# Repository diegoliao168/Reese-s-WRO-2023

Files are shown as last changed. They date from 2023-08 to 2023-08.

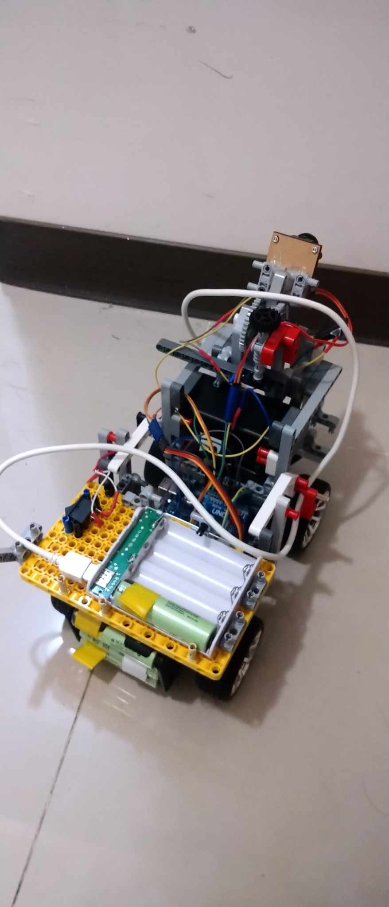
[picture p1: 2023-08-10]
v-photo/363670610_1052829679035555_8030239496635746678_n.jpg

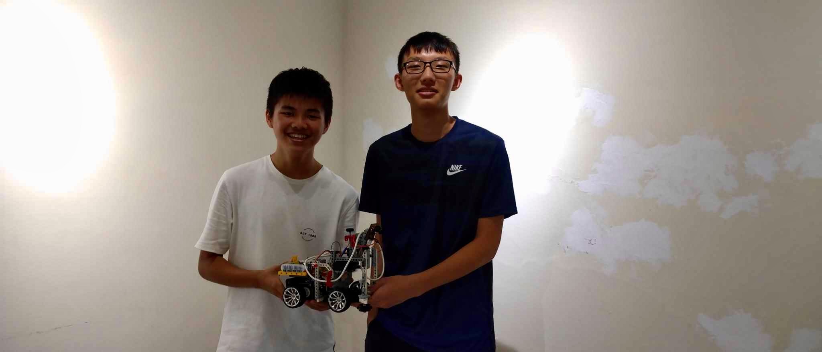
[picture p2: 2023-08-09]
t-photo/363800676_1494674244676651_163518513958916830_n.jpeg

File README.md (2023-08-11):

# Reese's

# 移動性管理

我們的機器人是採用與汽車相同的轉向邏輯和驅動方式。在前輪部分我們使用伺服馬達來控制我們的轉向機構，後輪的部分我們使用的是直流馬達。我們採用的是Arduino的Uno版和OpenMV的H7，Arduino的主要功用與控制轉向的伺服馬達溝通和後輪的直流馬達進行溝通。OpenMV的功用就像我們人的眼睛，透過影相辨識的方式來達到跟Arduino溝通控制車哪時轉向和哪時加速或減速。

在選擇馬達的時候我們找到兩種適合我們使用的馬達分別有4000rpm負載500公克的馬達和320rpm負載1500公克的馬達，考慮到我們的小車可能會需要拖動較大的載重。我們選擇了320rpm轉速的馬達負載1500公克的馬達。這顆馬達的型號為GA25-370、工作電壓六到十二伏特、功率2.5瓦、額定電流0.65安培、齒輪箱速比1:32.2。馬達之後有加速齒比帶動傳動軸來帶動後輪的兩顆輪子。

在前輪的部分我們選擇使用精準控制轉向角度的伺服馬達是MG996R。MG996R
工作電壓4.8V-7.2V、空載工作電流120mA。

因為一開始購買車輛的時候廠家沒有設計放電池的地方。因此我們3D列印了一塊在車子後的背板，為的就是能讓我們到電池有地方可以固定


# 電源和感測器管理
接下來是我們的車體結構是與市售的商家購買的，但是經過我們的改裝我們的車輛已經與市售的截然不同。我們車體裝上支架為了OpenMV和電池盒有辦法固定。應為電力不足得原因我們在車商裝了三套電池系統。第一套十二伏電池系統是供應主要的驅動馬達，接下來第二套八伏特的電池是供應給車上主要的溝通系統Arduino也是供應給前輪的轉向系統的伺服馬達，最後一套第三套四伏特的電池系統是給OpenMV單獨供電的為了讓OpenMV提供更穩定的訊息傳輸。

要讓我們與程式Arduino正確溝通我們需要Arduino IDE，Arduino IDE使與的程式語言是C語言透過C語言的溝通，我們的Arduino才能跟OpenMV和其他馬達傳送正確的指令。接下來OpenMV所使用的語言是Micro Python，Micro Python對我們來講是個全新的語言。當我們一開始使用的時候，我們一邊詢問我們的指導老師一遍看網路上的教學影片。開始撰寫OpenMV的程式從一開始的調顏色數值到顏色追蹤和如何用影像辨識距離。我們在寫OpenMV的程式時遇到最大的困難是在我們調顏色數值的時後，顏色數值可能會應為些微的燈光變化而有所不同。我們不得不反覆測試直到調到一個較好的數值。

原先我們使用的控制板是Arduino的Nano版經過我們的測試我們發現使用Nano版的時候Nano版的供電系統會不足以支撐兩顆馬達同時驅動，使轉向系統的伺服馬達無法轉到目標位子。經過測試後我們採用供電比較穩定的Arduino的Uno版，對支援更穩定的供電和更加優良的擴充。

經過我們的反覆測發現到原本8伏特的電池來去推動馬達的時後馬達的功率無法驅動我們的車。接下來我們就把原本的電壓乘以二到了十六伏特，但是我們沒有意識到我們所使用Arduino Uno的只能對應到十二伏特的電壓。應此我們燒壞了一塊主機板。經過這次經驗我們換了新的十二伏電池盒。也是因為改回了十二伏的電池，讓我們的機器人正常的執行任務，以及進行接下來的測試和實驗。

# 障礙管理
程式想法

先把轉彎角度、直走的速度、轉彎速度的角度都先歸零，直走伺服馬達的角度是固定的所以先放入變數還有每個顏色的閥值都是先量好放入變數，迴圈內的變數是每進行一次就要歸零。

當我們吧畫面正中央的第三等分跟第四等分來運算時我們可以透過畫面中的Y軸來判斷我們的車輛是否離牆面近而判斷是否轉彎並且修正。Y軸在畫面中越低就代表車輛離牆面越近，再來就傳送轉彎角度和馬達速度給Arduino Uno來進行轉彎。

如何判斷我們車輛應該轉逆時針還是順時針，我們運用到影像辨識來判斷橘色線的角度，大於90要轉左邊，小於90要轉右邊，這樣一來我們就可以知道每次轉彎是轉左邊還是右邊，但是影像辨識很容易受到燈光的影響，所以我們也試了很多方式來解決這個問題，也調了很多次閥值。

OpenMV
```
import sensor, image, time, math
from pyb import UART

threshold_index = 0

thresholds_black = [(38, 0, 100, -50, 74, -30)]
thresholds_red = [(8, 56, 127, 11, -128, 127)]
thresholds_green = [(25, 17, -24, -4, -28, 13)]
thresholds_blue = [(18, 45, 27, -7, -103, -7)]
thresholds_orange = [(47, 100, 71, 9, 127, -105)]

sensor.reset()
sensor.set_pixformat(sensor.RGB565)
sensor.set_framesize(sensor.QVGA)
sensor.skip_frames(time = 2000)
sensor.set_auto_gain(False)
sensor.set_auto_whitebal(False)
clock = time.clock()
uart = UART(3, 19200)
m = 0
angle = 0    #轉彎角度
mot_1 = 200  #轉彎PWM
mot_2 = 200   #直走PWM
middle = 95  #伺服馬達中間值

while(True):

    x3 = 0
    x4 = 0
    y3 = 0
    y4 = 0
    two_m = 0
    two = 0

    clock.tick()
    img = sensor.snapshot()
    #找橘色
    if m == 0 :
        for blob in img.find_blobs([thresholds_orange[0]], pixels_threshold=400, area_threshold=400, merge=True):

            if blob.elongation() > 0.5:
                #img.draw_edges(blob.min_corners(), color=(255,0,0))
                img.draw_line(blob.major_axis_line(), color=(0,255,0))
                print( blob.rotation_deg())    #把線的角度算出來
                m = blob.rotation_deg()    #方進m這個變數
                #img.draw_line(blob.minor_axis_line(), color=(0,0,255))
                print (m)
                print (clock)
                if m > 90:  #判斷要轉左邊還是右邊

                    angle = 65 #左
                else :
                    angle = 125 #右

    threemax_x = 0
    threemax_y = 0
    #畫面三找黑色並把他框出來
    for blob in img.find_blobs([thresholds_black[threshold_index]], pixels_threshold=200, area_threshold=200, merge=True,roi=(108,0,54,250)):

        '''
        if blob.elongation() > 0.5:
            img.draw_edges(blob.min_corners(), color=(255,0,0))
            img.draw_line(blob.major_axis_line(), color=(0,255,0))
            img.draw_line(blob.minor_axis_line(), color=(0,0,255))
        '''
        if blob.cy() > threemax_y:     #找出y最大的框
            threemax_x = blob.cx()
            threemax_y = blob.cy()
    img.draw_rectangle(blob.rect())
    img.draw_cross(blob.cx(), blob.cy())
    x3 = threemax_x
    y3 = threemax_y

    img.draw_keypoints([(blob.cx(), blob.cy(), int(math.degrees(blob.rotation())))], size=20)
    if  threemax_y > 100:
        uart.write(str(mot_1)+","+ str(angle)+"E\n")
        time.sleep_ms(20)
    else:
        uart.write(str(mot_2)+","+ str(middle)+"E\n")
        time.sleep_ms(20)

    fourmax_x = 0
    fourmax_y = 0
    #畫面四找黑色並把他框出來
    for blob in img.find_blobs([thresholds_black[threshold_index]], pixels_threshold=200, area_threshold=200, merge=True,roi=(162,0,54,250)):

        '''
        if blob.elongation() > 0.5:
            img.draw_edges(blob.min_corners(), color=(255,0,0))
            img.draw_line(blob.major_axis_line(), color=(0,255,0))
            img.draw_line(blob.minor_axis_line(), color=(0,0,255))
        '''
        if blob.cy() > fourmax_y:     #找出Y最大的框
            fourmax_x = blob.cx()
            fourmax_y = blob.cy()
    img.draw_rectangle(blob.rect())
    img.draw_cross(blob.cx(), blob.cy())
    x4 = fourmax_x
    y4 = fourmax_y
    if fourmax_y > 100:
        uart.write(str(mot_1)+","+ str(angle)+"E\n")
        time.sleep_ms(20)
    else:
        uart.write(str(mot_2)+","+ str(middle)+"E\n")
        time.sleep_ms(20)

    img.draw_keypoints([(blob.cx(), blob.cy(), int(math.degrees(blob.rotation())))], size=20)
    
```
程式想法

先把腳位、變數、輸出、電壓設定好把變數都歸零。開始速度的運算，運算完之後運算轉向角。接下來寫上防呆程式。

Arduino

      #include <Servo.h>
      int Speed=0,angle=100,cnt=0;
      char c[15]={0}; 
      Servo S;
      void setup() {
       // put your setup code here, to run once:
       S.attach(9);
       Serial.begin(19200);
       pinMode(4,OUTPUT);
       pinMode(5,OUTPUT);
       pinMode(6,OUTPUT);
       digitalWrite(4,LOW);
       digitalWrite(5,HIGH);
     }

     void loop() {
       // put your main code here, to run repeatedly:

       if (Serial.available()) {//收序列資料
     // Read the most recent byte
     c[cnt] = Serial.read();
     if(c[cnt] == 10)
     {
        Speed = 0;
        angle = 0;
        cnt = 0;
        int i=0;
        //////////////////////////////////////
        while(c[i]!=',')
        {
          i++;
        }
        for(int k=0;k<i;k++)//逗號前加
        {
            Speed = Speed*10+(c[k]-48);
           
        }
        int ii=0;
        while(c[ii]!='E')
        {
          ii++;
        }
        for(int k=i+1;k<ii;k++)//逗號後加
        {
            angle = angle*10+(c[k]-48);
        }
        ////////////////////////////////////
        if(angle>125){
          angle=125;//右轉防呆
        }
        if(angle<65){
          angle=65;//左轉防呆
          }
         if(Speed>220){
          Speed=160;//速度防呆
         }
         
        analogWrite(6,Speed);
        S.write(angle);
     }

     cnt++;
    
       }
   
     }
右轉防呆跟左轉防呆的用意在於防止OpenMV在跟Arduino溝通的時候，傳錯訊號導致前輪轉向的伺服馬達卡死，而影響後續的行走過程。

速度防呆也是一樣防止溝通上的錯誤導致車輛暴衝導致撞到障礙物或是撞到牆壁。

在斜線匡起來的部分中代表每當速度或是角度在當前的位數時乘十可以進到下下一格位數這時候需要家上原本的數字。需要減掉48是因為ASCII碼0=48所以我們把算出來的ASCII碼減掉48就是我們要的數字了。

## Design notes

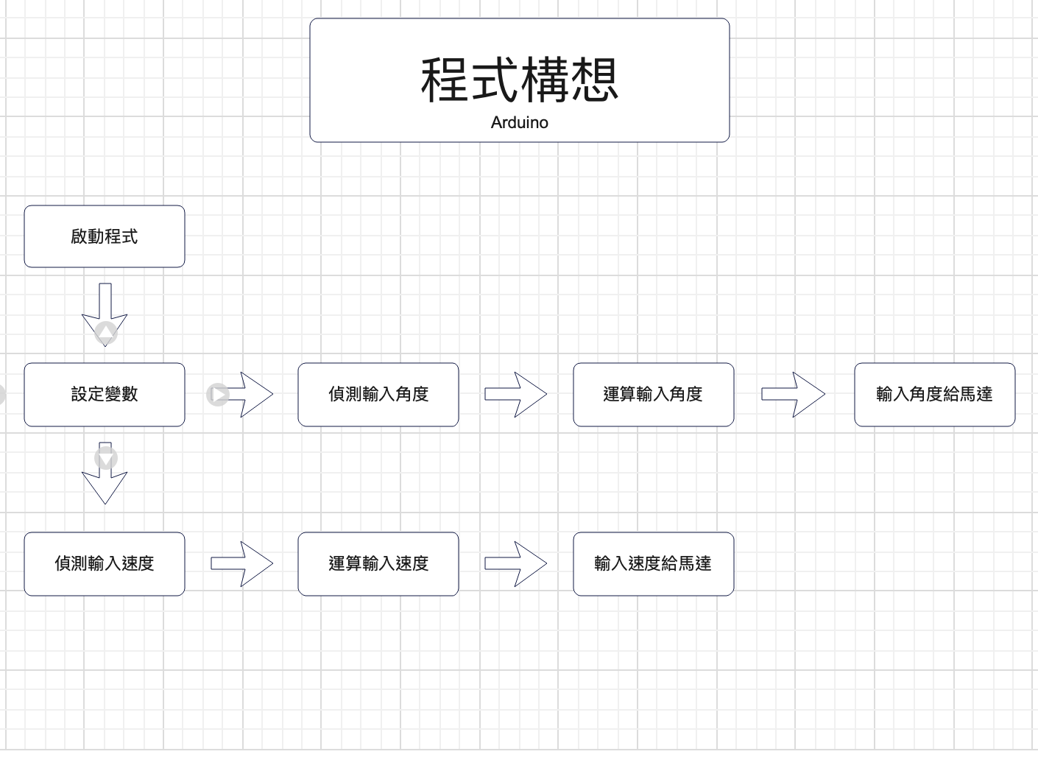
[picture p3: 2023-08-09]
Other/Arduino程式構想.png

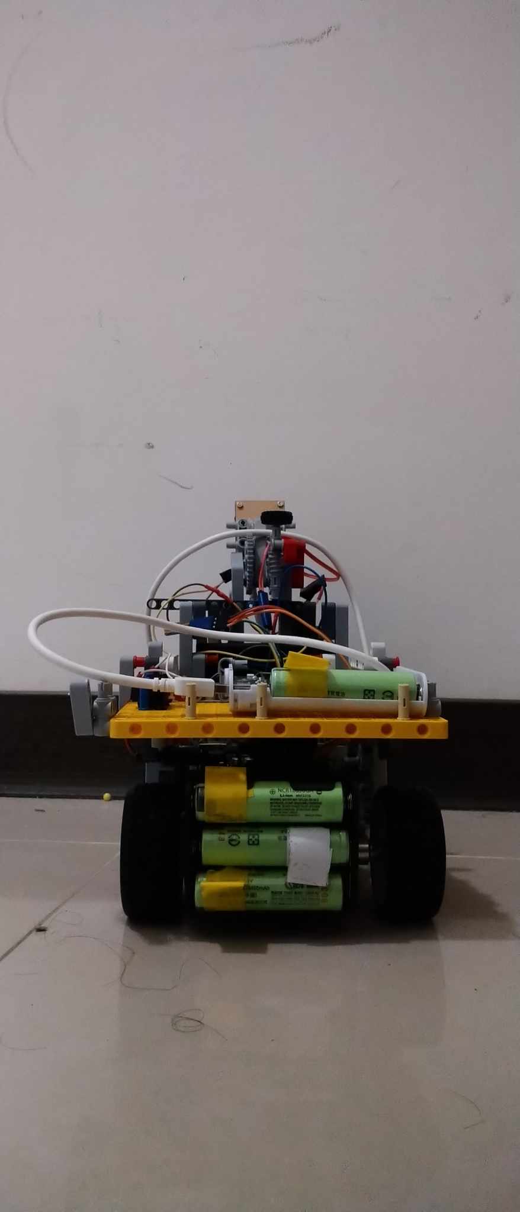
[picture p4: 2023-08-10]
v-photo/359672807_3026557870822477_8788263900361719581_n.jpg

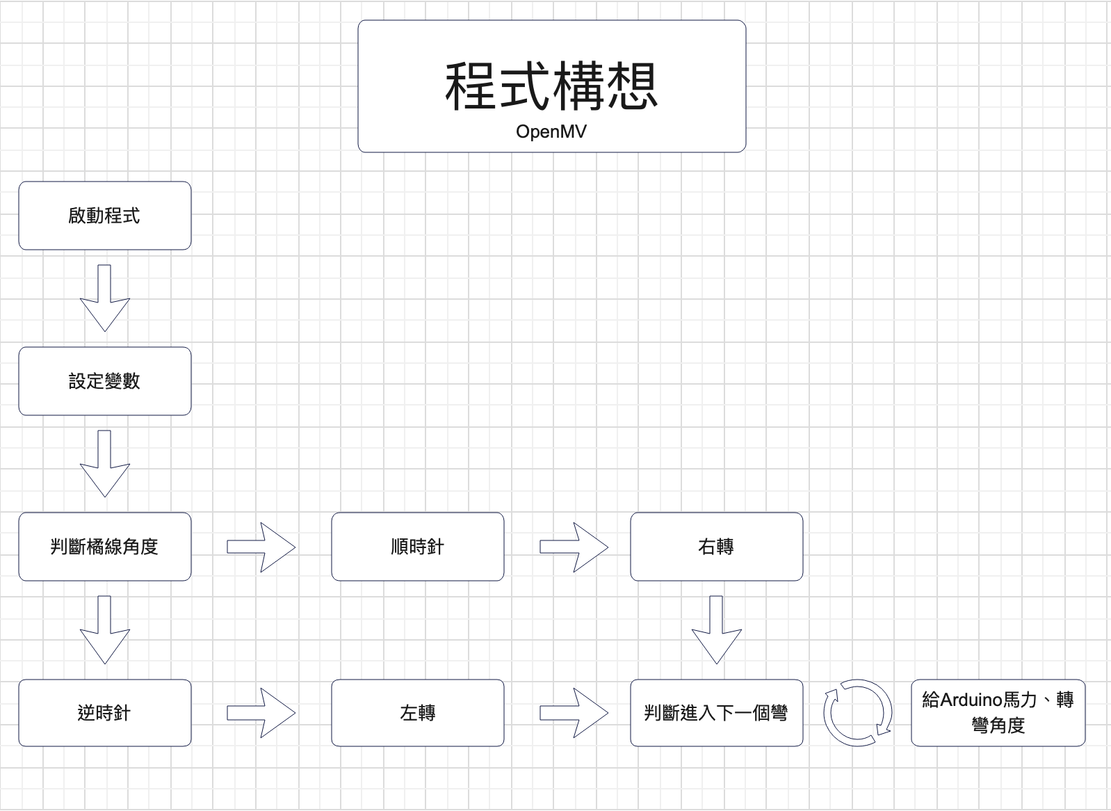
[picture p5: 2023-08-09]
Other/OpenMV程式構想.png

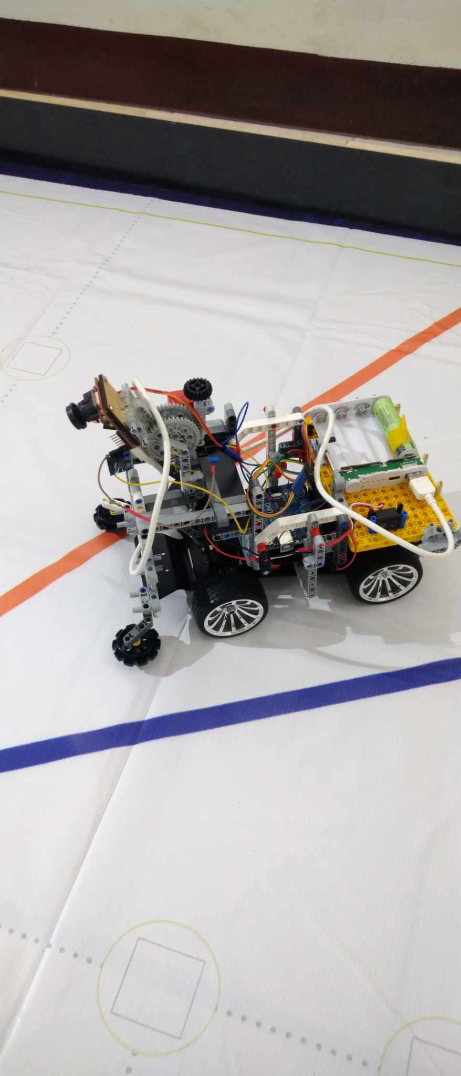
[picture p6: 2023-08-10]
v-photo/363578091_937215540705117_7346094950045631902_n.jpg

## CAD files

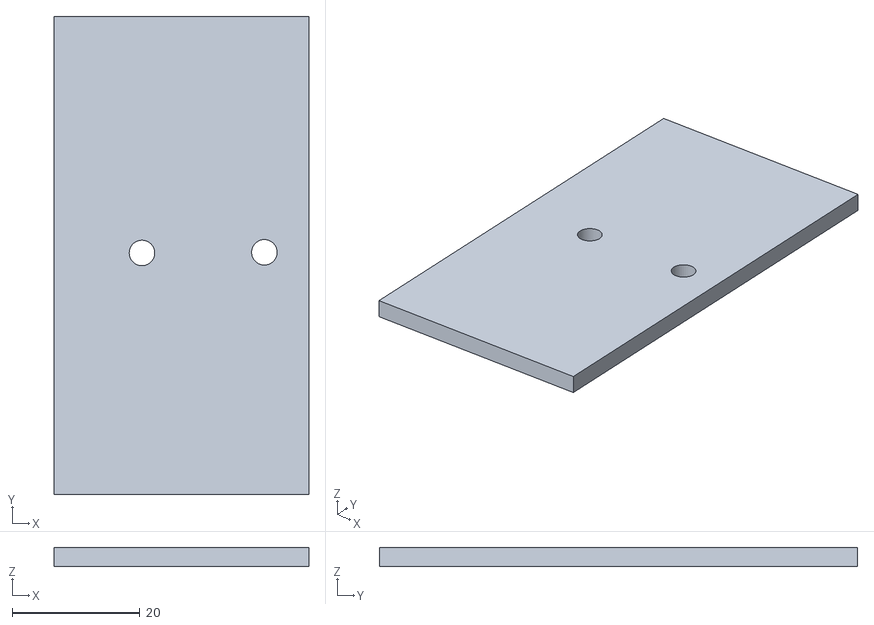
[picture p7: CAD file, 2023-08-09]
models/battery holder.stl
40.0 x 75.0 x 3.00
